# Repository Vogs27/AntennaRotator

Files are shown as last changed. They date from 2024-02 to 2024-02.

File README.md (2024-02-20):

# AntennaRotator
This is an improved antenna rotor based on [Satnogs Project rotor V3.1](https://wiki.satnogs.org/SatNOGS_Rotator_v3). It uses the same mechanics but a different custom made controller.

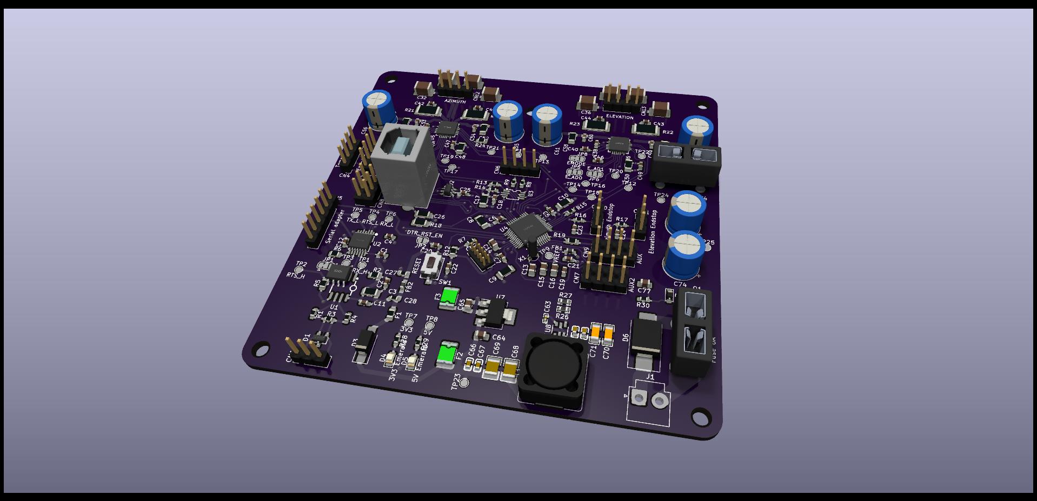
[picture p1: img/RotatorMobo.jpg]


The board uses an ARM based microcontroller (SAMD21) at 48MHz, giving more headroom for future developements. It uses the Arduino Zero core to ease the programming stage. 
TMC2209 are used as drivers to provide a silent experience.

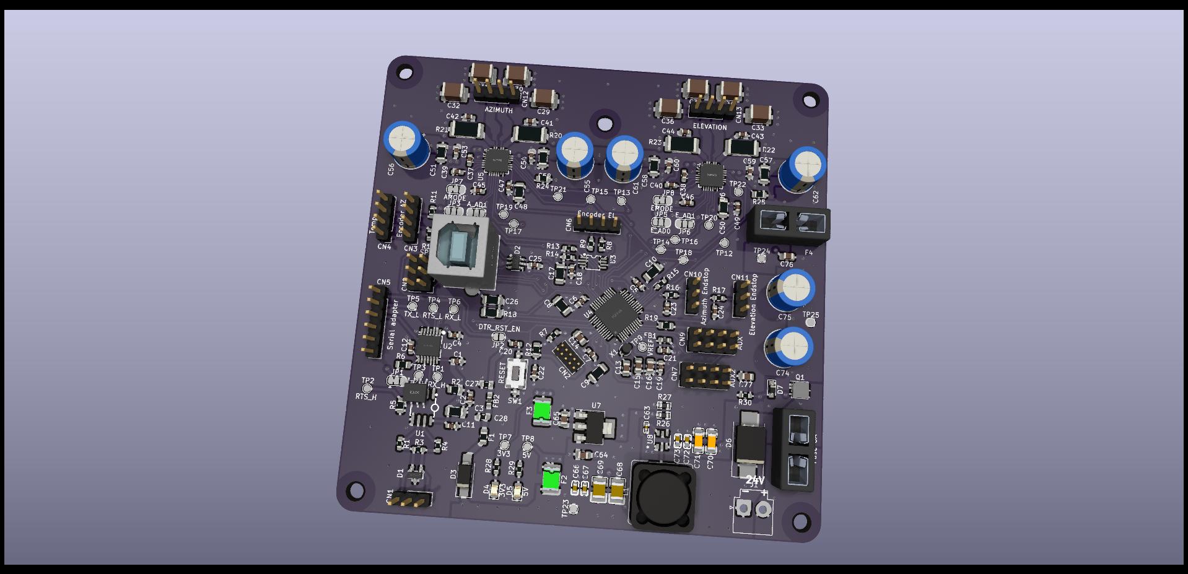
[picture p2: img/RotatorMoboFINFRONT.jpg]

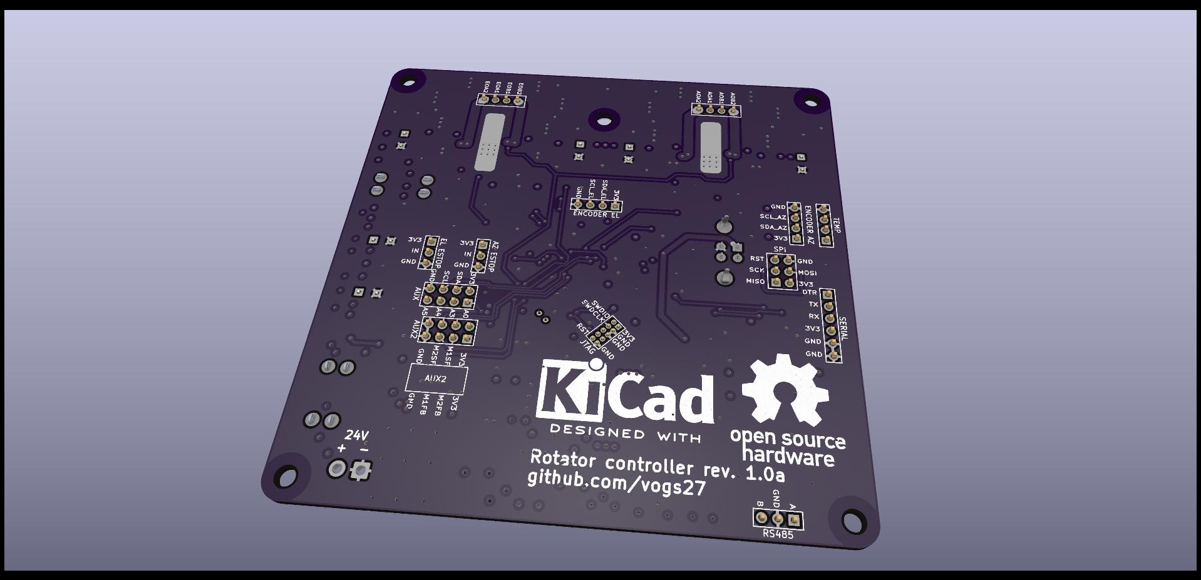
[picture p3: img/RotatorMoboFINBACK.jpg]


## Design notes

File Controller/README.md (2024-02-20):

# Controller board

This is the first version of the controller board.
It's a 100mmx100mm 4 layer PCB.

An interactive bom is provided inside ibom folder.
Grbl files are in production folder together with a BOM file. Some LCSC components code are provided for reference.

The board was manufactured at JLCPCB.

## ToDo

Ground trace in TMC2209 is not connected to both ground vias but just to one. After testing this doesn't seems a problem.

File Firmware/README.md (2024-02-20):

# Rotator Firmware

This firmware is based on [SatNOGS Rotator Controller](https://gitlab.com/librespacefoundation/satnogs/satnogs-rotator-firmware) and is in a very alpha state: use it with caution!
A lot of safety features are still not implemented (watchdog, overheating protection).

## Instructions

In order to use this code, you need to install:
 * [AccelStepper library](http://www.airspayce.com/mikem/arduino/AccelStepper/index.html)
 * [TMCStepper library](https://github.com/teemuatlut/TMCStepper)
 * Download Arduino IDE (tested with 1.8.5)

#### Burn optiboot

Only with SWD programming:

* Jlink like programmer
* Arduino Micro as DAP device

Connect the programmer to the SWD port on the board. Using Arduino IDE, select Arduino Zero (programming port), then burn bootloader. Wait while flashing the bootloader and disconnect the programmer.

#### Upload the code

Connect a USB cable to the controller board. Select Arduino Zero (native port) in Arduino IDE. Open the main firmware file (.ino) in Arduino IDE and press Upload. Wait while flashing the firmware. Disconnect USB cable.

## Testing with hamlib - rotctl or with Serial Monitor

Connect the PC with contreller via RS485 to USB by using the right converter.
Use commands of rotctl:

```
rotctl -m 204 -s 19200 -r /dev/ttyUSB1 -vvvvv
```

Replace the /dev/ttyUSB1 with the device which is connected to PC.

Use commands of easycomm 3:

Send directly commands of easycomm 3 as described in Easycomm implemantation section.

## Use with Gpredict
Configure Gpredict and launch hamlib deamon with: 
```
rotctld -m 202 -r COM7 -s 19200 -T 127.0.0.1 -t 4533 -C timeout=500 -C retry=0 > pause
```
Replace the COM7 with the device which is connected to PC.

## Easycomm implemantation

* AZ, Azimuth, number - 1 decimal place [deg]
* EL, Elevation, number - 1 decimal place [deg]
* SA, Stop azimuth moving
* SE, Stop elevation moving
* RESET, Move to home position
* PARK, Move to park position
* IP, Read an input, number
    * Temperature = 0
    * SW1 = 1
    * SW2 = 2
    * Encoder1 = 3
    * Encoder2 = 4
    * Load of M1/AZ = 5
    * Load of M2/EL = 6
    * Speed of M1/AZ (DPS) = 7
    * Speed of M2/EL (DPS) = 8
* VE, Request Version
* GS, Get status register, number
    * idle = 1
    * moving = 2
    * pointing = 4
    * error = 8
* GE, Get error register, number
    * no_error = 1
    * sensor_error = 2
    * homing_error = 4
    * motor_error = 8
    * over_temperature = 12
    * wdt_error = 16
* VL, Velocity Left ,number [mdeg/s]
* VR, Velocity Right, number [mdeg/s]
* VU, Velocity Up, number [mdeg/s]
* VD, Velocity Down, number [mdeg/s]
* CR, Read config, register [0-x]
    * Gain P for M1/AZ = 1
    * Gain I for M1/AZ = 2
    * Gain D for M1/AZ = 3
    * Gain P for M2/EL = 4
    * Gain I for M2/EL = 5
    * Gain D for M2/EL = 6
    * Azimuth park position = 7
    * Elevation park position = 8
    * Control mode (position = 0, speed = 1) = 9
* CW, Write config, register [0-x]
    * Gain P for M1/AZ = 1
    * Gain I for M1/AZ = 2
    * Gain D for M1/AZ = 3
    * Gain P for M2/EL = 4
    * Gain I for M2/EL = 5
    * Gain D for M2/EL = 6
    * Azimuth park position = 7
    * Elevation park position = 8
    * This reg is set from Vx commands control mode (position = 0, speed = 1) = 9
* RB, command to reboot controller

## Pins Configuration

```
M1IN1 10, Step or PWM1
M1IN2 9, Direction or PWM2
M1SF  7, Status flag
M1FB  A1, Load measurment

M2IN1 11, Step or PWM1
M2IN2 3, Direction or PWM2
M2SF  6, Status flag
M2FB  A0, Load measurment

MOTOR_EN 8, Enable/Disable motors

SW1 5, Endstop for axis 1
SW2 4, Endstop for axis 2

RS485_DIR 2, RS485 Half Duplex direction pin

SDA_PIN 3, Data I2C pin
SCL_PIN 4, Clock I2C pin

PIN12 12, Digital output pin
PIN13 13, Digital output pin
A2    A2, Analog input pin
A3    A3, Analog input pin
```

## TODO

* Implement overheating protection and overheating warning
* Implement watchdog
* Replace blocking delay with non-blocking delay in easycomm implementation.
* Remove PID related stuff (not used with steppers)

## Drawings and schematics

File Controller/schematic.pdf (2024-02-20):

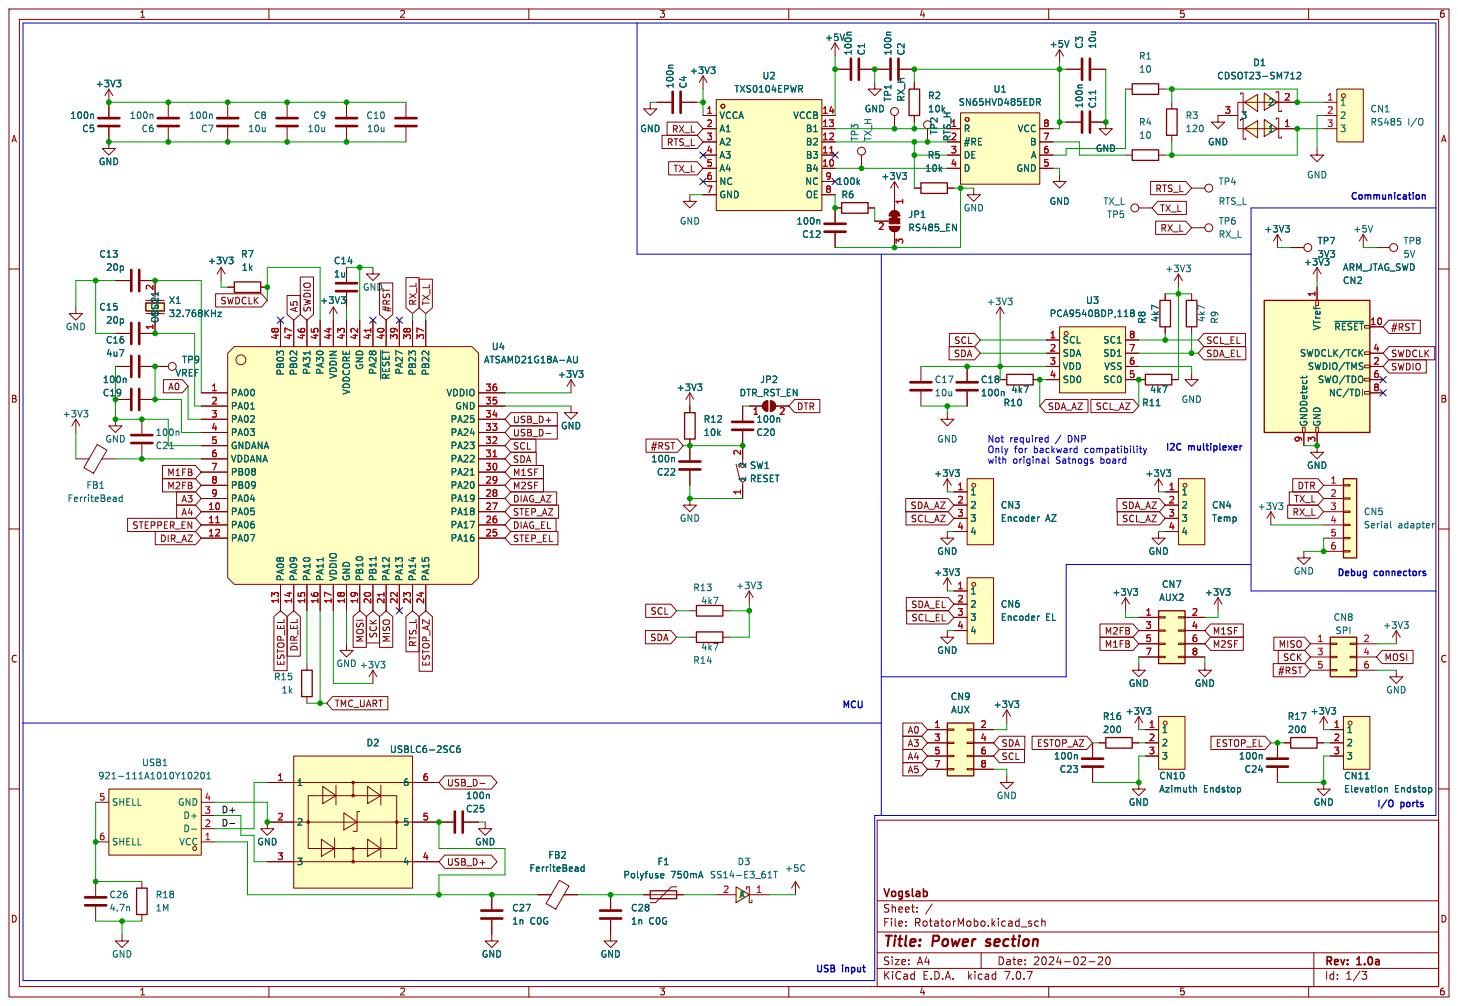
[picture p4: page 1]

3 SWDCLK/TCK 4 SWO/TDO 6 NC/TDI 8 GNDDetect 9 CN2 ARM_JTAG_SWD +3V3 C21

3 SWDCLK/TCK 4 SWO/TDO 6 NC/TDI 8 GNDDetect 9 +3V3 GND

File: RotatorMobo.kicad_sch Sheet: / Vogslab

Id: 1/3 Title: Power section

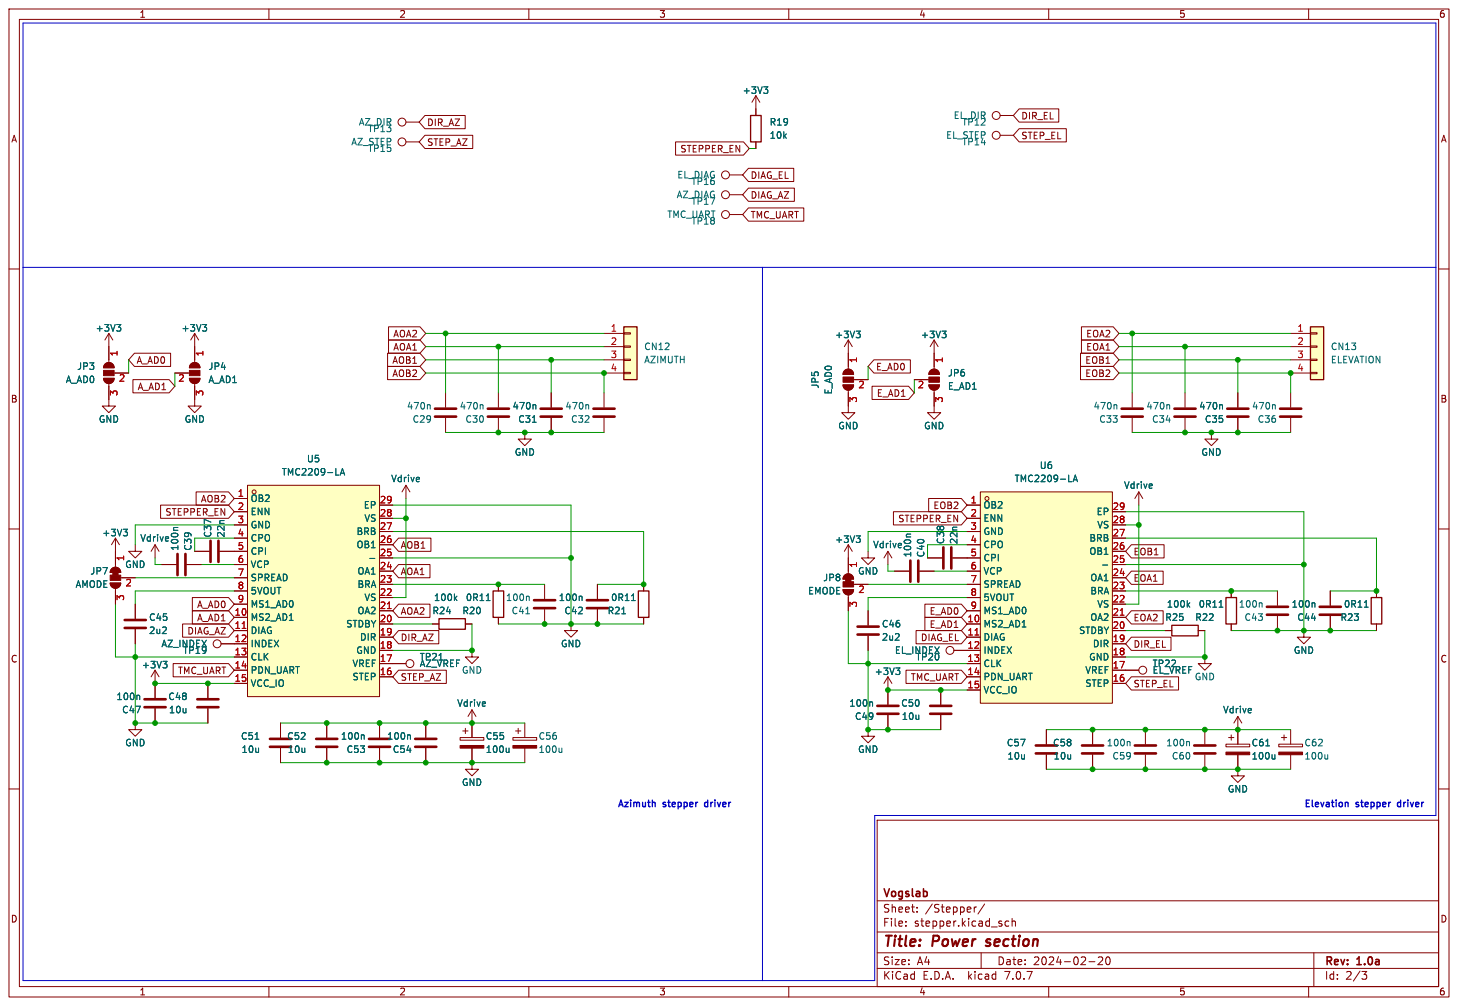
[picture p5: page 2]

- 25 OB1 26 BRB 27 VS 28 EP 29 GND 3 CPO 4 CPI 5 VCP 6 SPREAD 7

File: stepper.kicad_sch Sheet: /Stepper/
Id: 2/3 Title: Power section

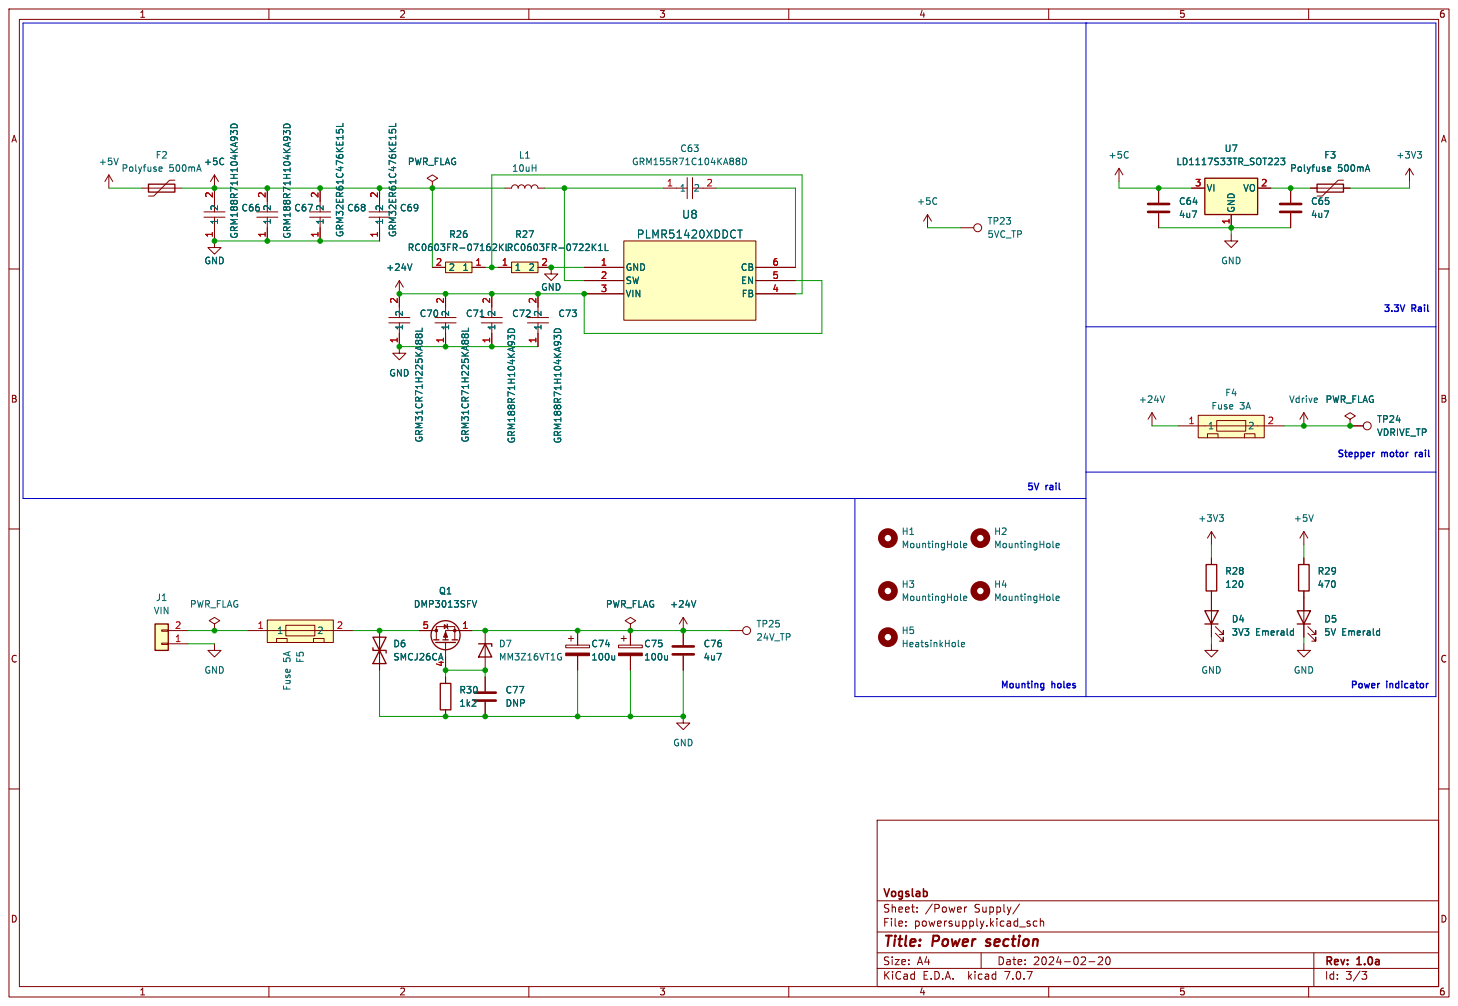
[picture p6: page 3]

Id: 3/3 Title: Power section

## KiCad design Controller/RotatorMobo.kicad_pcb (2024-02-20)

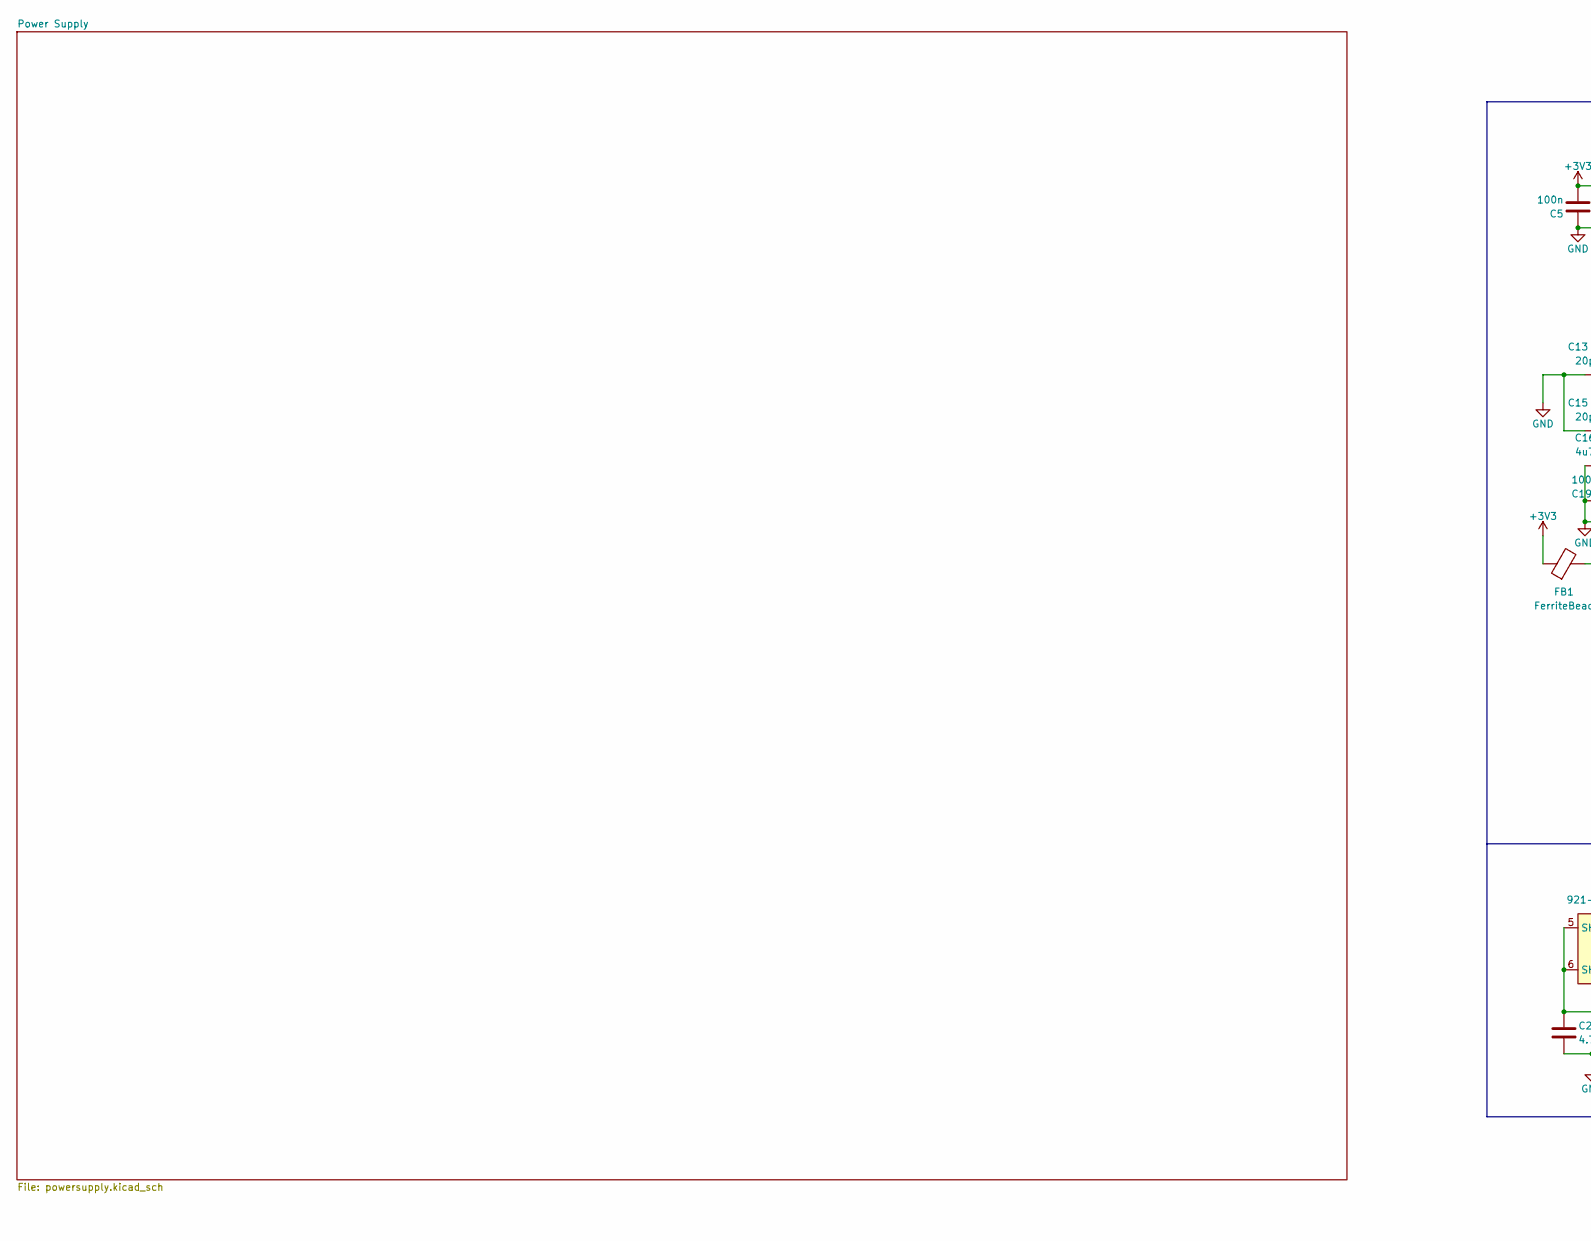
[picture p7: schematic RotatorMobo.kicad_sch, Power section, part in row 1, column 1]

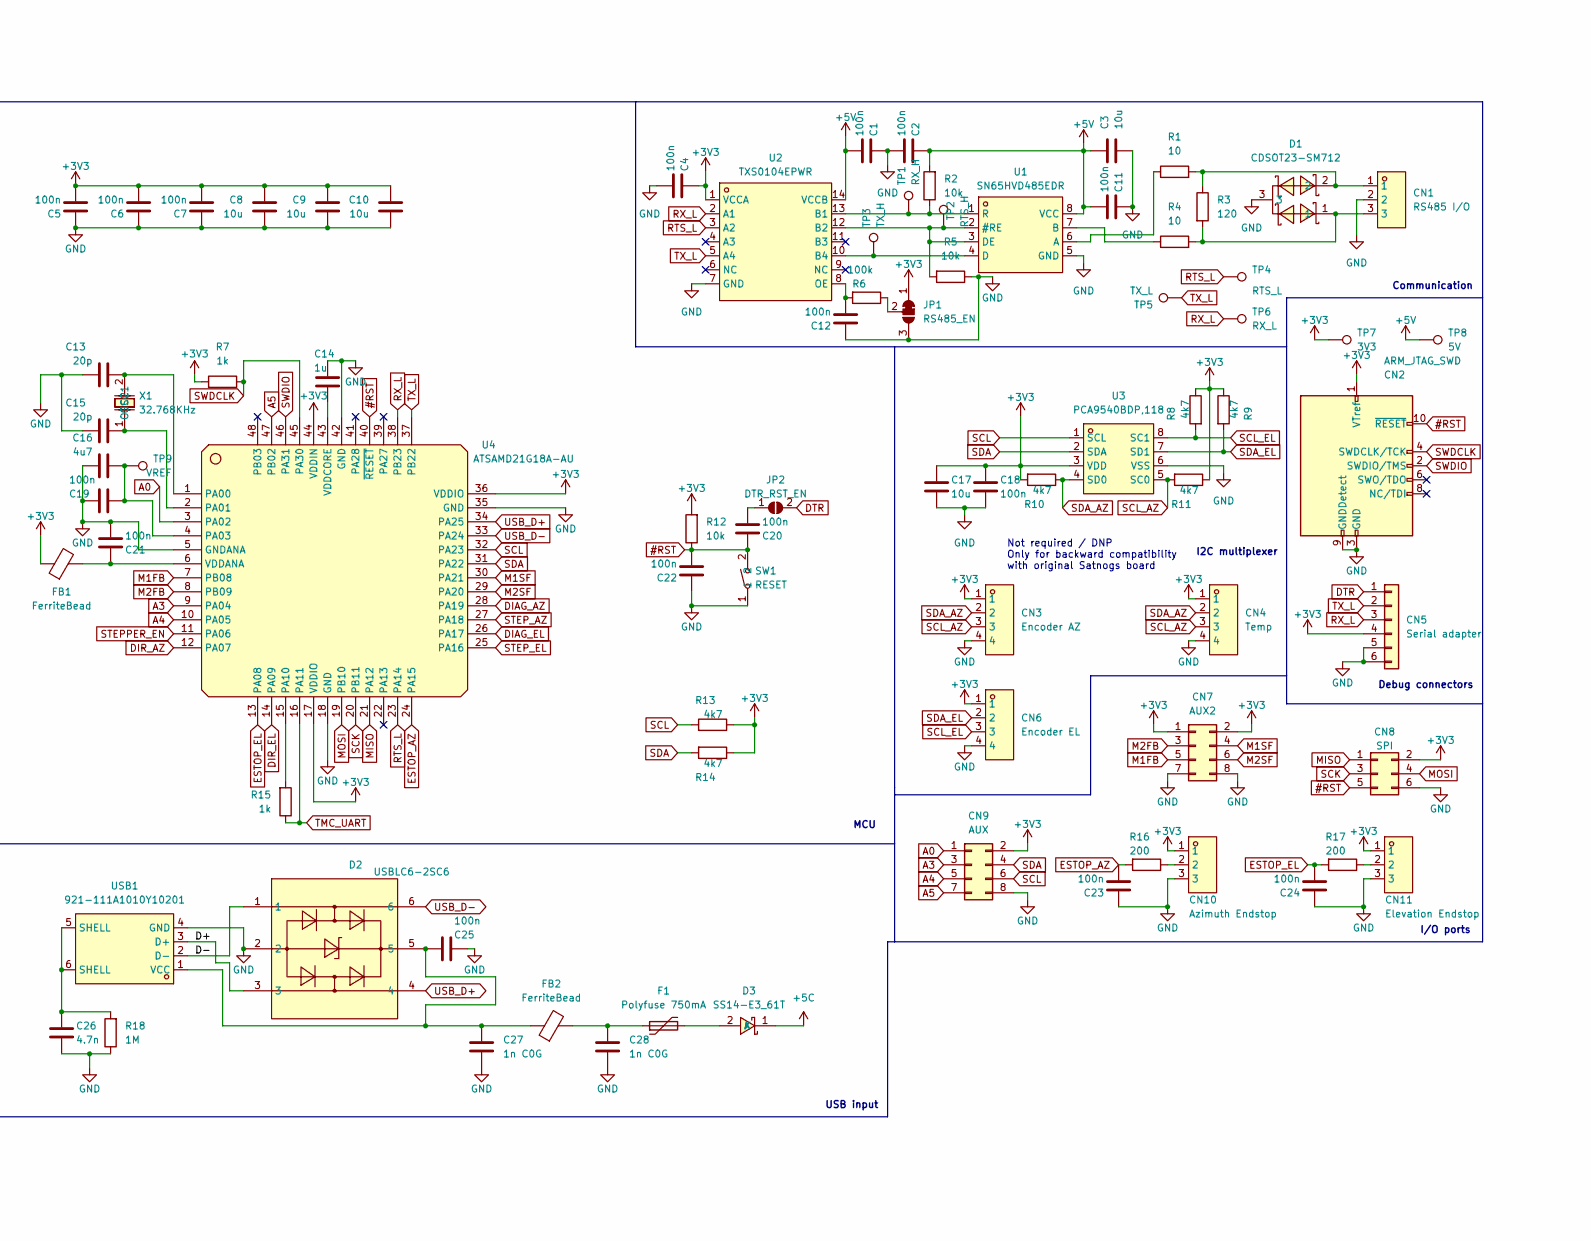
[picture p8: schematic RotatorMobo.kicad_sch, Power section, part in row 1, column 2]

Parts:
C1, C2, C4, C5, C6, C7, C11, C12, C18, C19, C20, C21, C22, C23, C24, C25: 100n; C_0603_1608Metric_Pad1.08x0.95mm_HandSolder; LCSC_id C1591
C3, C8, C9, C10, C17: 10u; R_1206_3216Metric_Pad1.30x1.75mm_HandSolder; LCSC_id C89632
C13, C15: 20p; C_0805_2012Metric_Pad1.18x1.45mm_HandSolder; LCSC_id C1798
C14: 1u; C_0805_2012Metric_Pad1.18x1.45mm_HandSolder; LCSC_id C116352
C16: 4u7; C_0805_2012Metric_Pad1.18x1.45mm_HandSolder; LCSC_id C98192
C26: 4.7n; R_1206_3216Metric_Pad1.30x1.75mm_HandSolder; LCSC_id C571063
C27, C28: 1n C0G; R_0603_1608Metric_Pad0.98x0.95mm_HandSolder; LCSC_id C3909020
CN1: RS485 I/O; PinHeader_1x03_P2.54mm_Vertical; LCSC Part C5341202
CN2: ARM_JTAG_SWD; PinHeader_2x05_P1.27mm_Vertical
CN3: Encoder AZ; PinHeader_1x04_P2.54mm_Vertical; LCSC Part C722867
CN4: Temp; PinHeader_1x04_P2.54mm_Vertical; LCSC Part C722867
CN5: Serial adapter; PinHeader_1x06_P2.54mm_Vertical
CN6: Encoder EL; PinHeader_1x04_P2.54mm_Vertical; LCSC Part C722867
CN7: AUX2; PinHeader_2x04_P2.54mm_Vertical
CN8: SPI; PinHeader_2x03_P2.54mm_Vertical
CN9: AUX; PinHeader_2x04_P2.54mm_Vertical
CN10: Azimuth Endstop; PinHeader_1x03_P2.54mm_Vertical; LCSC Part C5341202
CN11: Elevation Endstop; PinHeader_1x03_P2.54mm_Vertical; LCSC Part C5341202
D1: CDSOT23-SM712; SOT-23_L2.9-W1.3-P1.90-LS2.4-BR; LCSC Part C404012
D2: USBLC6-2SC6; SOT-23-6_L2.9-W1.6-P0.95-LS2.8-BL; LCSC Part C7519
D3: SS14-E3_61T; D_SMA_Handsoldering; LCSC Part C47460
F1: Polyfuse 750mA; Fuse_0805_2012Metric_Pad1.15x1.40mm_HandSolder; LCSC_id C883111
FB1, FB2: FerriteBead; L_0603_1608Metric_Pad1.05x0.95mm_HandSolder; MPN BLM18PG471SN1; LCSC ID C97853
JP1: RS485_EN; SolderJumper-3_P1.3mm_Bridged12_RoundedPad1.0x1.5mm
JP2: DTR_RST_EN; SolderJumper-2_P1.3mm_Open_RoundedPad1.0x1.5mm
R1, R4: 10; R_0603_1608Metric_Pad0.98x0.95mm_HandSolder; LCSC_id C22859
R2, R5, R12: 10k; R_0805_2012Metric_Pad1.20x1.40mm_HandSolder; LCSC_id C25612
R3: 120; R_0603_1608Metric_Pad0.98x0.95mm_HandSolder; LCSC_id C2906988
R6: 100k; R_0805_2012Metric_Pad1.20x1.40mm_HandSolder; LCSC_id C25611
R7, R15: 1k; R_0603_1608Metric_Pad0.98x0.95mm_HandSolder; LCSC_id C21190
R8, R9, R10, R11, R13, R14: 4k7; R_0603_1608Metric_Pad0.98x0.95mm_HandSolder; LCSC_id C25999
R16, R17: 200; R_0603_1608Metric_Pad0.98x0.95mm_HandSolder; LCSC_id C103389
R18: 1M; R_1206_3216Metric_Pad1.30x1.75mm_HandSolder; LCSC_id C175518
SW1: RESET; SW-SMD_L6.1-W3.5-LS8.0; LCSC Part C5117870
TP1: RX_H; TestPoint_Pad_D1.5mm
TP2: RTS_H; TestPoint_Pad_D1.5mm
TP3: TX_H; TestPoint_Pad_D1.5mm
TP4: RTS_L; TestPoint_Pad_D1.5mm
TP5: TX_L; TestPoint_Pad_D1.5mm
TP6: RX_L; TestPoint_Pad_D1.5mm
TP7: 3V3; TestPoint_Pad_D1.5mm
TP8: 5V; TestPoint_Pad_D1.5mm
TP9: VREF; TestPoint_Pad_D1.5mm
U1: SN65HVD485EDR; SOIC-8_L5.0-W4.0-P1.27-LS6.0-BL; LCSC Part C27899
U2: TXS0104EPWR; TSSOP-14_L5.0-W4.4-P0.65-LS6.4-BL; LCSC Part C44955
U3: PCA9540BDP,118; TSSOP-8_L3.0-W3.0-P0.65-LS4.9-BL; LCSC Part C2652901
U4: ATSAMD21G18A-AU; TQFP-48_L7.0-W7.0-P0.50-LS9.0-BL; LCSC Part C78624
USB1: 921-111A1010Y10201; USB-B-TH_921-111A1010Y10201; LCSC Part C2763094
X1: 32.768KHz; OSC-TH_BD1.9-P0.70; LCSC Part C403947

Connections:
#RST: C20.2, C22.1, CN2.10 (~RESET), CN8.5, R12.1, SW1.2, U4.40 (~RESET)
+3V3: C4.2, C5.1, C6.1, C7.1, C8.2, C9.2, C10.2, C17.2, C18.2, CN2.1 (VTref), CN3.1, CN4.1, CN5.4, CN6.1, CN7.1, CN7.2, CN8.2, CN9.2, CN10.1, CN11.1, FB1.1, JP1.1 (A), R7.2, R8.1, R9.1, R10.2, R11.1, R12.2, R13.1, R14.1, TP7.1, U2.1 (VCCA), U3.3 (VDD), U4.17 (VDDIO), U4.36 (VDDIO), U4.44 (VDDIN); also elsewhere on the board
+5C: D3.1 (K); also elsewhere on the board
+5V: C1.1, C2.2, C3.2, C11.1, R2.2, TP8.1, U1.8 (VCC), U2.14 (VCCB); also elsewhere on the board
/D+: D2.3, USB1.3 (D+)
/D-: D2.1, USB1.2 (D-)
A0: CN9.1, U4.3 (PA02)
A3: CN9.3, U4.9 (PA04)
A4: CN9.5, U4.10 (PA05)
A5: CN9.7, U4.47 (PB02)
DIAG_AZ: U4.28 (PA19); also elsewhere on the board
DIAG_EL: U4.26 (PA17); also elsewhere on the board
DIR_AZ: U4.12 (PA07); also elsewhere on the board
DIR_EL: U4.14 (PA09); also elsewhere on the board
DTR: CN5.1, JP2.2 (B)
ESTOP_AZ: C23.1, R16.2, U4.24 (PA15)
ESTOP_EL: C24.1, R17.2, U4.13 (PA08)
GND: C1.2, C2.1, C3.1, C4.1, C5.2, C6.2, C7.2, C8.1, C9.1, C10.1, C11.2, C12.2, C13.1, C14.2, C15.1, C16.1, C17.1, C18.1, C19.1, C21.1, C22.2, C23.2, C24.2, C25.2, C26.1, C27.1, C28.1, CN1.2, CN2.3 (GND), CN2.5 (GND), CN2.9 (GNDDetect), CN3.4, CN4.4, CN5.5, CN5.6, CN6.4, CN7.7, CN7.8, CN8.6, CN9.8, CN10.3, CN11.3, D1.3, D2.2, JP1.3 (B), R5.1, R18.1, SW1.1, U1.5 (GND), U2.7 (GND), U3.6 (VSS), U4.5 (GNDANA), U4.18 (GND), U4.35 (GND), U4.42 (GND), USB1.4 (GND); also elsewhere on the board
M1FB: CN7.5, U4.7 (PB08)
M1SF: CN7.4, U4.30 (PA21)
M2FB: CN7.3, U4.8 (PB09)
M2SF: CN7.6, U4.29 (PA20)
MISO: CN8.1, U4.21 (PA12)
MOSI: CN8.4, U4.19 (PB10)
unnamed: C26.2, R18.2, USB1.5 (SHELL), USB1.6 (SHELL)
unnamed: C28.2, F1.1, FB2.2
unnamed: CN1.1, D1.2, R1.2, R3.1
unnamed: CN1.3, D1.1, R3.2, R4.2
unnamed: CN10.2, R16.1
unnamed: CN11.2, R17.1
unnamed: D3.2 (A), F1.2
unnamed: JP1.2 (C), R6.1
unnamed: C20.1, JP2.1 (A)
unnamed: R5.2, TP2.1, U1.2 (#RE), U1.3 (DE), U2.12 (B2)
unnamed: R1.1, U1.6 (A)
unnamed: R4.1, U1.7 (B)
unnamed: TP3.1, U1.4 (D), U2.10 (B4)
unnamed: R2.1, TP1.1, U1.1 (R), U2.13 (B1)
unnamed: C12.1, R6.2, U2.8 (OE)
unnamed: C13.2, U4.1 (PA00), X1.2 (OSC2)
unnamed: C15.2, U4.2 (PA01), X1.1 (OSC1)
unnamed: C16.2, C19.2, TP9.1, U4.4 (PA03)
unnamed: R15.2, U4.15 (PA10)
unnamed: C21.2, FB1.2, U4.6 (VDDANA)
unnamed: C14.1, U4.43 (VDDCORE)
unnamed: C25.1, C27.2, D2.5, FB2.1, USB1.1 (VCC)
RTS_L: TP4.1, U2.3 (A2), U4.23 (PA14)
RX_L: CN5.3, TP6.1, U2.2 (A1), U4.38 (PB23)
SCK: CN8.3, U4.20 (PB11)
SCL: CN9.6, R13.2, U3.1 (SCL), U4.32 (PA23)
SCL_AZ: CN3.3, CN4.3, R11.2, U3.5 (SC0)
SCL_EL: CN6.3, R8.2, U3.8 (SC1)
SDA: CN9.4, R14.2, U3.2 (SDA), U4.31 (PA22)
SDA_AZ: CN3.2, CN4.2, R10.1, U3.4 (SD0)
SDA_EL: CN6.2, R9.2, U3.7 (SD1)
STEPPER_EN: U4.11 (PA06); also elsewhere on the board
STEP_AZ: U4.27 (PA18); also elsewhere on the board
STEP_EL: U4.25 (PA16); also elsewhere on the board
SWDCLK: CN2.4 (SWDCLK/TCK), R7.1, U4.45 (PA30)
SWDIO: CN2.2 (SWDIO/TMS), U4.46 (PA31)
TMC_UART: R15.1, U4.16 (PA11); also elsewhere on the board
TX_L: CN5.2, TP5.1, U2.5 (A4), U4.37 (PB22)
USB_D+: D2.4, U4.34 (PA25)
USB_D-: D2.6, U4.33 (PA24)

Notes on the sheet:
Communication
I2C multiplexer
Debug connectors
I/O ports
MCU
USB input
Not required / DNP Only for backward compatibility with original Satnogs board

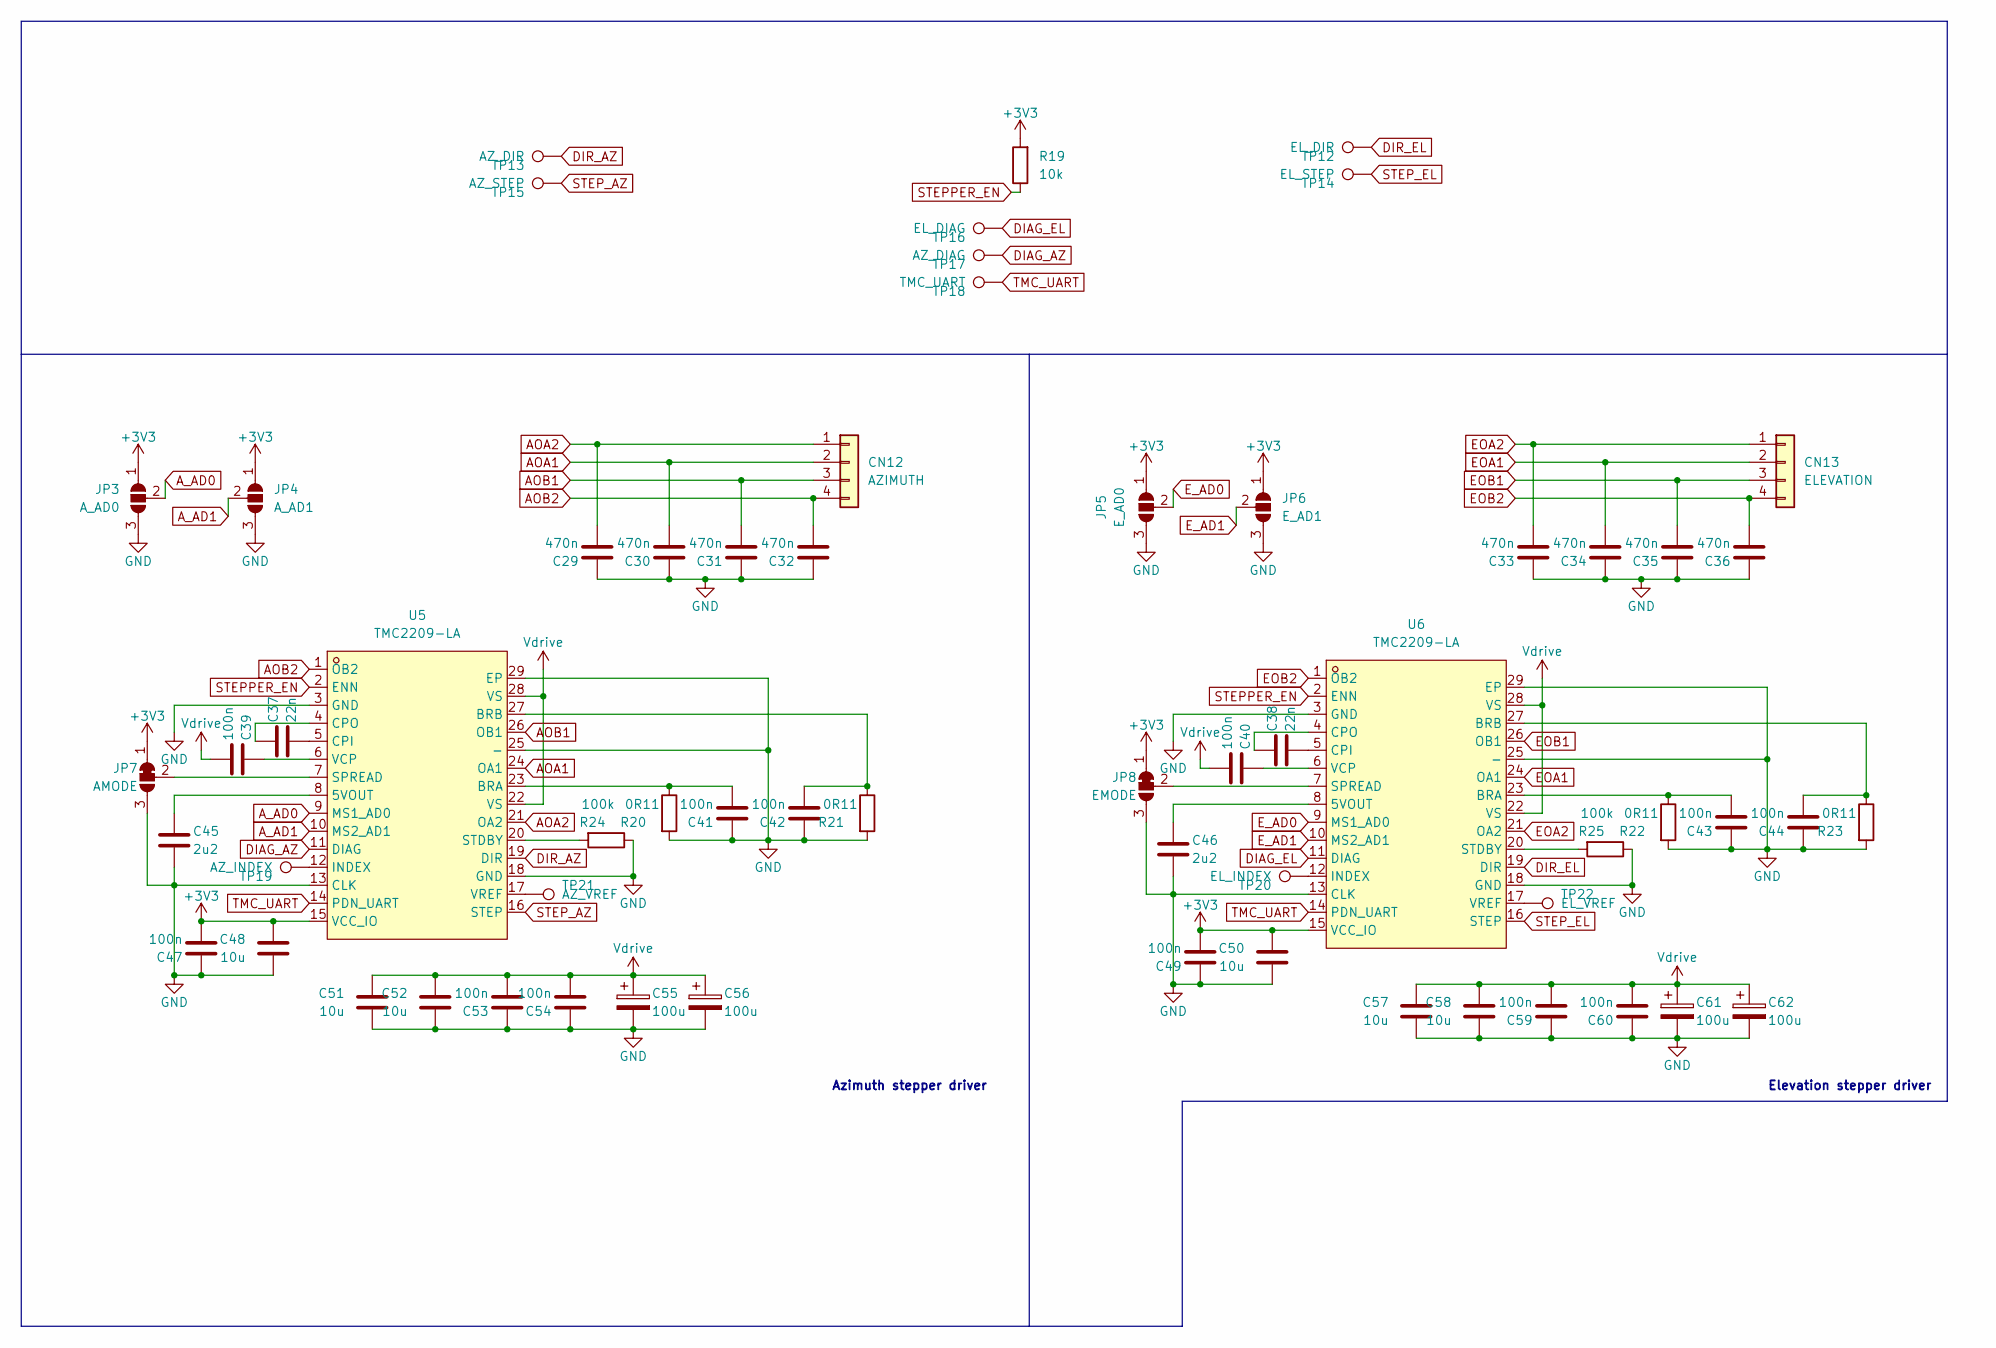
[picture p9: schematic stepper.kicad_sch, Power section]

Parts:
C29, C30, C31, C32, C33, C34, C35, C36: 470n; C_1812_4532Metric_Pad1.57x3.40mm_HandSolder; LCSC_id C152994
C37, C38: 22n; C_0603_1608Metric_Pad1.08x0.95mm_HandSolder; LCSC_id C21122
C39, C40, C41, C42, C43, C44, C47, C49, C53, C54, C59, C60: 100n; C_0603_1608Metric_Pad1.08x0.95mm_HandSolder; LCSC_id C1591
C45, C46: 2u2; C_0603_1608Metric_Pad1.08x0.95mm_HandSolder; LCSC_id C23630
C48, C50, C51, C52, C57, C58: 10u; R_1206_3216Metric_Pad1.30x1.75mm_HandSolder; LCSC_id C89632
C55, C56, C61, C62: 100u; CP_Radial_D8.0mm_P3.50mm
CN12: AZIMUTH; PinHeader_1x04_P2.54mm_Vertical
CN13: ELEVATION; PinHeader_1x04_P2.54mm_Vertical
JP3: A_AD0; SolderJumper-3_P1.3mm_Open_RoundedPad1.0x1.5mm
JP4: A_AD1; SolderJumper-3_P1.3mm_Open_RoundedPad1.0x1.5mm
JP5: E_AD0; SolderJumper-3_P1.3mm_Open_RoundedPad1.0x1.5mm
JP6: E_AD1; SolderJumper-3_P1.3mm_Open_RoundedPad1.0x1.5mm
JP7: AMODE; SolderJumper-3_P1.3mm_Bridged12_RoundedPad1.0x1.5mm
JP8: EMODE; SolderJumper-3_P1.3mm_Bridged12_RoundedPad1.0x1.5mm
R19: 10k; R_0805_2012Metric_Pad1.20x1.40mm_HandSolder; LCSC_id C25612
R20, R21, R22, R23: 0R11; R_2512_6332Metric_Pad1.40x3.35mm_HandSolder; LCSC_id C333708
R24, R25: 100k; R_0805_2012Metric_Pad1.20x1.40mm_HandSolder; LCSC_id C25611
TP12: EL_DIR; TestPoint_Pad_D1.5mm
TP13: AZ_DIR; TestPoint_Pad_D1.5mm
TP14: EL_STEP; TestPoint_Pad_D1.5mm
TP15: AZ_STEP; TestPoint_Pad_D1.5mm
TP16: EL_DIAG; TestPoint_Pad_D1.5mm
TP17: AZ_DIAG; TestPoint_Pad_D1.5mm
TP18: TMC_UART; TestPoint_Pad_D1.5mm
TP19: AZ_INDEX; TestPoint_Pad_D1.5mm
TP20: EL_INDEX; TestPoint_Pad_D1.5mm
TP21: AZ_VREF; TestPoint_Pad_D1.5mm
TP22: EL_VREF; TestPoint_Pad_D1.5mm
U5, U6: TMC2209-LA; QFN-28_L5.0-W5.0-P0.50-BL-EP; LCSC Part C465949

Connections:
+3V3: C47.1, C48.2, C49.1, C50.2, JP3.1 (A), JP4.1 (A), JP5.1 (A), JP6.1 (A), JP7.1 (A), JP8.1 (A), R19.2, U5.15 (VCC_IO), U6.15 (VCC_IO); also elsewhere on the board
AOA1: C30.1, CN12.2, U5.24 (OA1)
AOA2: C29.1, CN12.1, U5.21 (OA2)
AOB1: C31.1, CN12.3, U5.26 (OB1)
AOB2: C32.1, CN12.4, U5.1 (OB2)
A_AD0: JP3.2 (C), U5.9 (MS1_AD0)
A_AD1: JP4.2 (C), U5.10 (MS2_AD1)
DIAG_AZ: TP17.1, U5.11 (DIAG); also elsewhere on the board
DIAG_EL: TP16.1, U6.11 (DIAG); also elsewhere on the board
DIR_AZ: TP13.1, U5.19 (DIR); also elsewhere on the board
DIR_EL: TP12.1, U6.19 (DIR); also elsewhere on the board
EOA1: C34.1, CN13.2, U6.24 (OA1)
EOA2: C33.1, CN13.1, U6.21 (OA2)
EOB1: C35.1, CN13.3, U6.26 (OB1)
EOB2: C36.1, CN13.4, U6.1 (OB2)
E_AD0: JP5.2 (C), U6.9 (MS1_AD0)
E_AD1: JP6.2 (C), U6.10 (MS2_AD1)
GND: C29.2, C30.2, C31.2, C32.2, C33.2, C34.2, C35.2, C36.2, C41.2, C42.2, C43.2, C44.2, C45.1, C46.1, C47.2, C48.1, C49.2, C50.1, C51.1, C52.1, C53.2, C54.2, C55.2, C56.2, C57.1, C58.1, C59.2, C60.2, C61.2, C62.2, JP3.3 (B), JP4.3 (B), JP5.3 (B), JP6.3 (B), JP7.3 (B), JP8.3 (B), R20.2, R21.2, R22.2, R23.2, R24.1, R25.1, U5.3 (GND), U5.13 (CLK), U5.18 (GND), U5.25 (-), U5.29 (EP), U6.3 (GND), U6.13 (CLK), U6.18 (GND), U6.25 (-), U6.29 (EP); also elsewhere on the board
unnamed: JP7.2 (C), U5.7 (SPREAD)
unnamed: JP8.2 (C), U6.7 (SPREAD)
unnamed: C45.2, U5.8 (5VOUT)
unnamed: C41.1, R20.1, U5.23 (BRA)
unnamed: C42.1, R21.1, U5.27 (BRB)
unnamed: C37.1, U5.5 (CPI)
unnamed: C37.2, U5.4 (CPO)
unnamed: TP19.1, U5.12 (INDEX)
unnamed: R24.2, U5.20 (STDBY)
unnamed: C39.2, U5.6 (VCP)
unnamed: TP21.1, U5.17 (VREF)
unnamed: C46.2, U6.8 (5VOUT)
unnamed: C43.1, R22.1, U6.23 (BRA)
unnamed: C44.1, R23.1, U6.27 (BRB)
unnamed: C38.1, U6.5 (CPI)
unnamed: C38.2, U6.4 (CPO)
unnamed: TP20.1, U6.12 (INDEX)
unnamed: R25.2, U6.20 (STDBY)
unnamed: C40.2, U6.6 (VCP)
unnamed: TP22.1, U6.17 (VREF)
STEPPER_EN: R19.1, U5.2 (ENN), U6.2 (ENN); also elsewhere on the board
STEP_AZ: TP15.1, U5.16 (STEP); also elsewhere on the board
STEP_EL: TP14.1, U6.16 (STEP); also elsewhere on the board
TMC_UART: TP18.1, U5.14 (PDN_UART), U6.14 (PDN_UART); also elsewhere on the board
Vdrive: C39.1, C40.1, C51.2, C52.2, C53.1, C54.1, C55.1, C56.1, C57.2, C58.2, C59.1, C60.1, C61.1, C62.1, U5.22 (VS), U5.28 (VS), U6.22 (VS), U6.28 (VS); also elsewhere on the board

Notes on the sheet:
Azimuth stepper driver
Elevation stepper driver

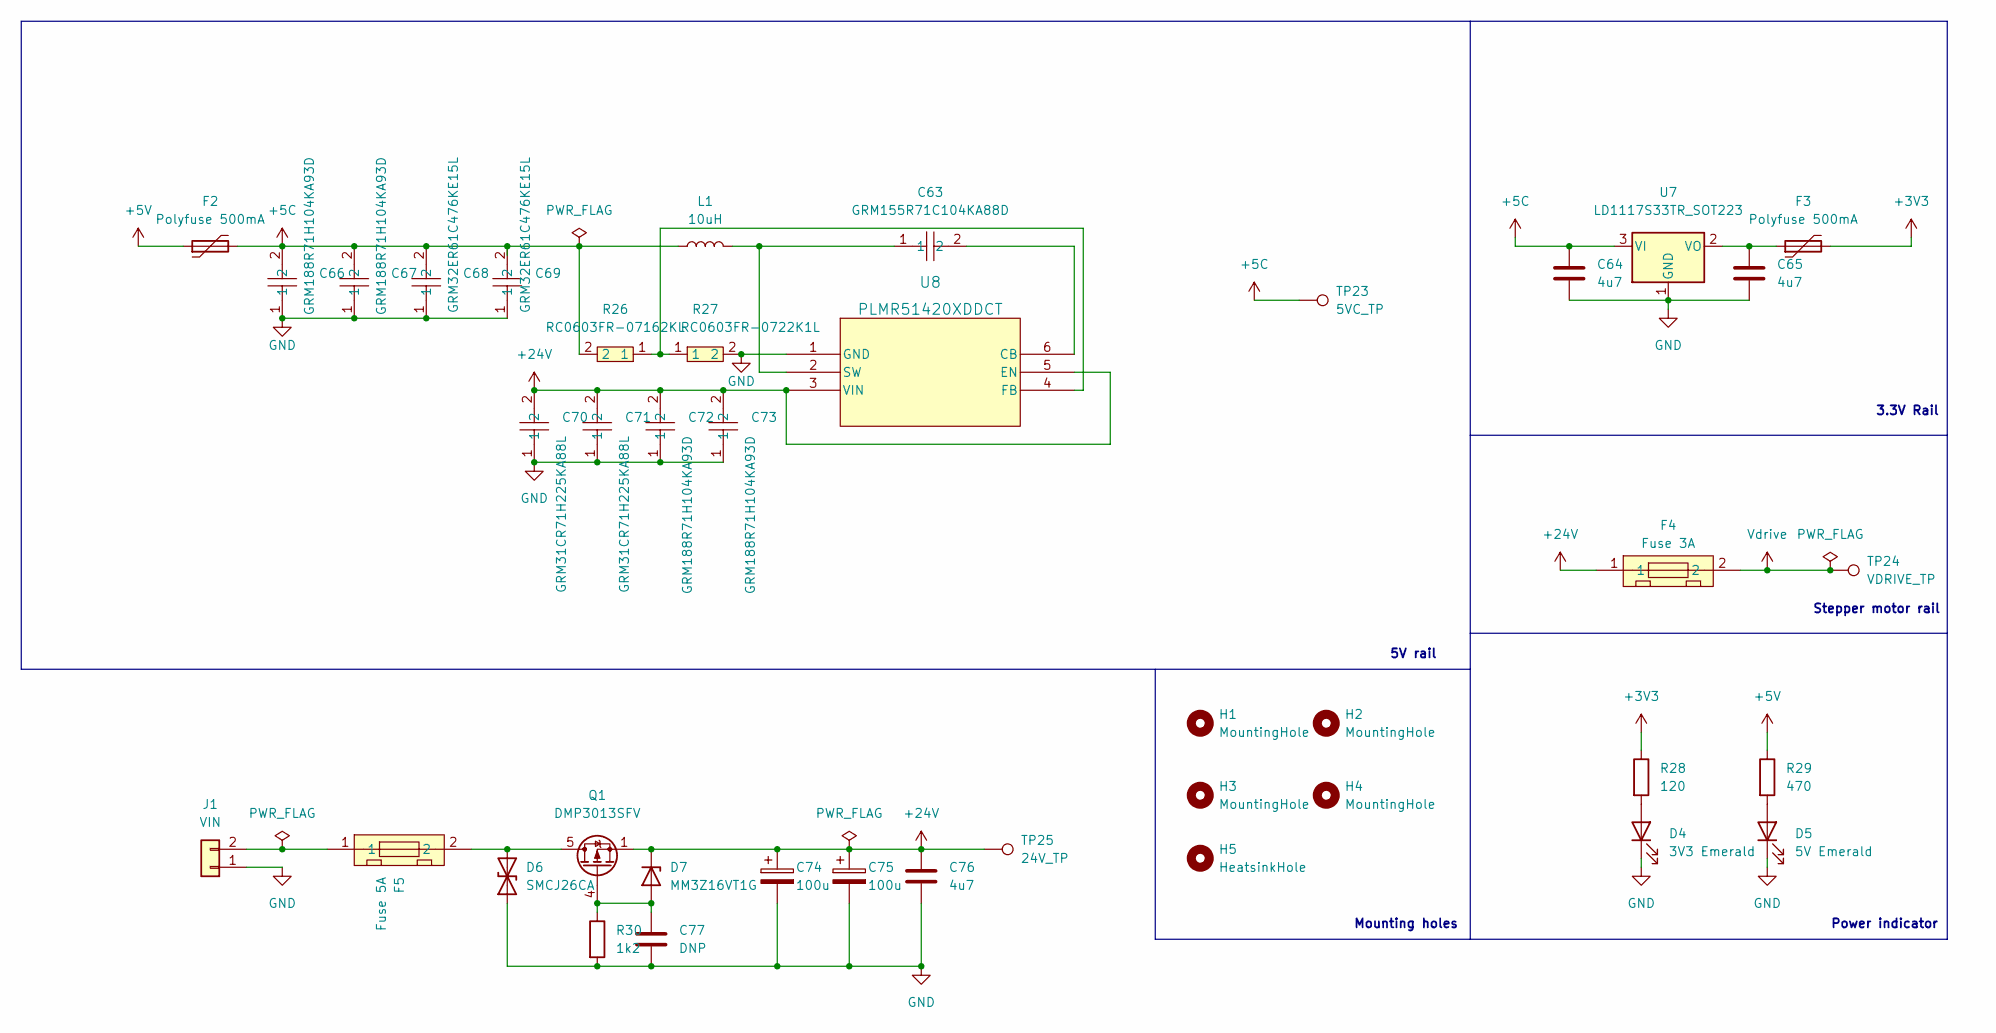
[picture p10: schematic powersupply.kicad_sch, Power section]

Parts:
C63: GRM155R71C104KA88D; C0402; LCSC Part C71629
C64, C65, C76: 4u7; C_0805_2012Metric_Pad1.18x1.45mm_HandSolder; LCSC_id C98192
C66, C67, C72, C73: GRM188R71H104KA93D; C0603; LCSC Part C77055
C68, C69: GRM32ER61C476KE15L; C1210; LCSC Part C77101
C70, C71: GRM31CR71H225KA88L; C1206; LCSC Part C77095
C74, C75: 100u; CP_Radial_D8.0mm_P3.50mm
C77: DNP; C_0805_2012Metric_Pad1.18x1.45mm_HandSolder
D4: 3V3 Emerald; LED_0805_2012Metric_Pad1.15x1.40mm_HandSolder; LCSC_id C965815
D5: 5V Emerald; LED_0805_2012Metric_Pad1.15x1.40mm_HandSolder; LCSC_id C965815
D6: SMCJ26CA; D_SMC_Handsoldering; LCSC_id C151280
D7: MM3Z16VT1G; D_SOD-323_HandSoldering; LCSC_id C150089
F2, F3: Polyfuse 500mA; Fuse_1812_4532Metric_Pad1.30x3.40mm_HandSolder; LCSC_id C2649901
F4: Fuse 3A; FUSE-TH_XF-506P; LCSC_id C2935468
F5: Fuse 5A; FUSE-TH_XF-506P; LCSC_id C2935468
H1, H2, H3, H4: MountingHole; MountingHole_3.2mm_M3
H5: HeatsinkHole; MountingHole_3.2mm_M3
J1: VIN; JST_VH_B2P-VH-B_1x02_P3.96mm_Vertical
L1: 10uH; L_Bourns_SRR1260; LCSC_id C2041557
Q1: DMP3013SFV; Diodes_PowerDI3333-8; LCSC_id C264098
R26: RC0603FR-07162KL; R0603; LCSC Part C165760
R27: RC0603FR-0722K1L; R0603; LCSC Part C137768
R28: 120; R_0603_1608Metric_Pad0.98x0.95mm_HandSolder; LCSC_id C2906988
R29: 470; R_0603_1608Metric_Pad0.98x0.95mm_HandSolder; LCSC_id C5140094
R30: 1k2; R_0603_1608Metric_Pad0.98x0.95mm_HandSolder; LCSC_id C25987
TP23: 5VC_TP; TestPoint_Pad_D1.5mm
TP24: VDRIVE_TP; TestPoint_Pad_D1.5mm
TP25: 24V_TP; TestPoint_Pad_D1.5mm
U7: LD1117S33TR_SOT223; SOT-223-3_TabPin2; LCSC_id C35879
U8: PLMR51420XDDCT; SOT-23-THIN-6_DDC_TEX; LCSC_id C5246146

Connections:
+3V3: F3.2, R28.1; also elsewhere on the board
+5C: C64.1, C66.2, C67.2, C68.2, C69.2, F2.2, L1.1, R26.2, TP23.1, U7.3 (VI); also elsewhere on the board
+5V: F2.1, R29.1; also elsewhere on the board
+24V: C70.2, C71.2, C72.2, C73.2, C74.1, C75.1, C76.1, D7.1 (K), F4.1, Q1.1 (S), Q1.2 (S), Q1.3 (S), TP25.1, U8.3 (VIN), U8.5 (EN)
GND: C64.2, C65.2, C66.1, C67.1, C68.1, C69.1, C70.1, C71.1, C72.1, C73.1, C74.2, C75.2, C76.2, C77.2, D4.1 (K), D5.1 (K), D6.1 (A1), J1.1, R27.2, R30.2, U7.1 (GND), U8.1 (GND); also elsewhere on the board
unnamed: D4.2 (A), R28.2
unnamed: D5.2 (A), R29.2
unnamed: D6.2 (A2), F5.2, Q1.5 (D)
unnamed: C77.1, D7.2 (A), Q1.4 (G), R30.1
unnamed: F5.1, J1.2
unnamed: C65.1, F3.1, U7.2 (VO)
unnamed: C63.2, U8.6 (CB)
unnamed: R26.1, R27.1, U8.4 (FB)
unnamed: C63.1, L1.2, U8.2 (SW)
Vdrive: F4.2, TP24.1; also elsewhere on the board

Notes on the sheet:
Stepper motor rail
5V rail
Mounting holes
3.3V Rail
Power indicator

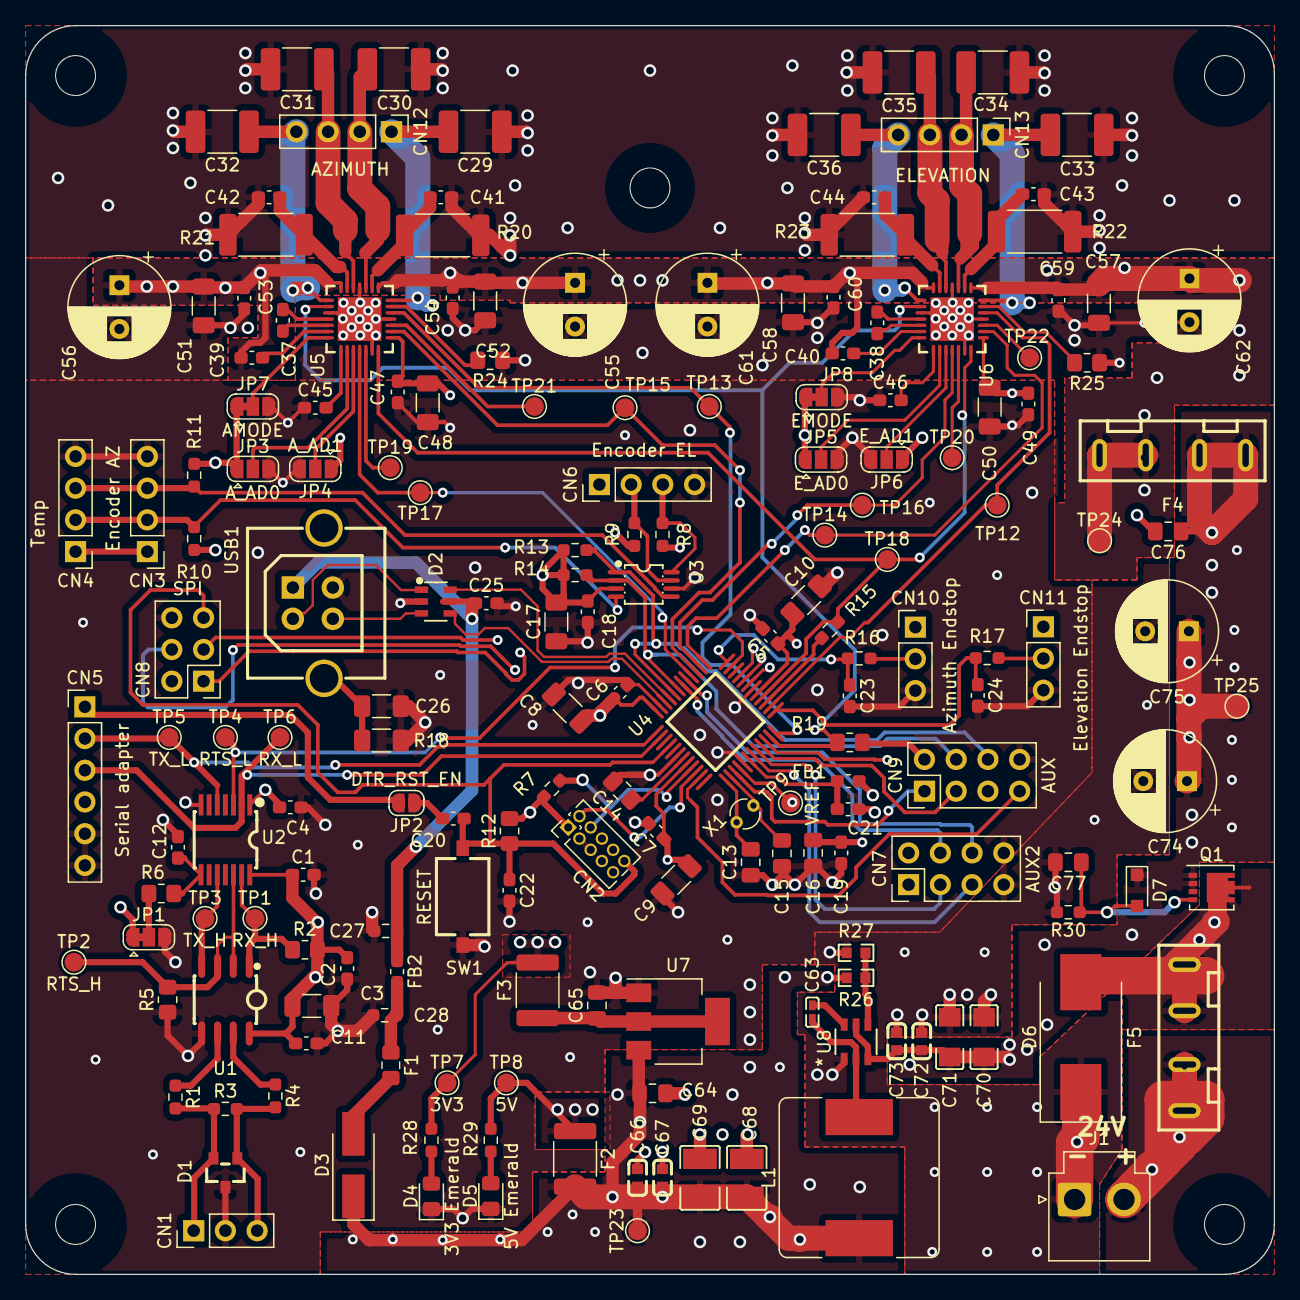
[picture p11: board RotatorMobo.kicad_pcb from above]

Board: 4 copper layers, 100.0 x 100.0 mm, 184 parts (0 on the bottom side), 107 nets.

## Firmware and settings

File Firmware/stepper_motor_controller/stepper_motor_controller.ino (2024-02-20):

/*!
   @file stepper_motor_controller.ino

   This is the documentation for satnogs rotator controller firmware
   for stepper motors configuration. The board (PCB) is placed in
   <a href="https://gitlab.com/librespacefoundation/satnogs/satnogs-rotator-controller">
   satnogs-rotator-controller </a> and is for releases:
   v2.0
   v2.1
   v2.2
   <a href="https://wiki.satnogs.org/SatNOGS_Rotator_Controller"> wiki page </a>

   @section dependencies Dependencies

   This firmware depends on <a href="http://www.airspayce.com/mikem/arduino/AccelStepper/index.htmlhttp://www.airspayce.com/mikem/arduino/AccelStepper/index.html">
   AccelStepper library</a> being present on your system. Please make sure you
   have installed the latest version before using this firmware.

   @section license License

   Licensed under the GPLv3.

*/

#define RATIO              54    ///< Gear ratio of rotator gear box
#define MICROSTEP          16     ///< Set Microstep
#define MIN_PULSE_WIDTH    1    ///< In microsecond for AccelStepper
#define MAX_SPEED          6400  ///< In steps/s, consider the microstep
#define MAX_ACCELERATION   3200  ///< In steps/s^2, consider the microstep
#define SPR                3200 ///< Step Per Revolution, consider the microstep 200steps(1.8 deg)*16microsteos
#define MIN_M1_ANGLE       0     ///< Minimum angle of azimuth
#define MAX_M1_ANGLE       360   ///< Maximum angle of azimuth
#define MIN_M2_ANGLE       0     ///< Minimum angle of elevation
#define MAX_M2_ANGLE       180   ///< Maximum angle of elevation
#define DEFAULT_HOME_STATE HIGH  ///< Change to LOW according to Home sensor
#define HOME_DELAY         12000 ///< Time for homing Deceleration in millisecond

#include <AccelStepper.h>
#include <TMCStepper.h>
#include <Wire.h>
#include "globals.h"
#include "easycomm.h"
#include "rotator_pins.h"
#include "rs485.h"
#include "endstop.h"
#include "watchdog.h"

uint32_t t_run = 0; // run time of uC

#define AZ_DRIVER_ADDRESS 0b00 // TMC2209 Driver address according to MS1 and MS2
#define EL_DRIVER_ADDRESS 0b01 // TMC2209 Driver address according to MS1 and MS2
#define R_SENSE 0.11f // Match to your driver


easycomm comm;
TMC2209Stepper driver_az(&Serial1, R_SENSE, AZ_DRIVER_ADDRESS);
TMC2209Stepper driver_el(&Serial1, R_SENSE, EL_DRIVER_ADDRESS);
AccelStepper stepper_az(1, M1IN1, M1IN2);
AccelStepper stepper_el(1, M2IN1, M2IN2); //stepper.DRIVER
endstop switch_az(SW1, DEFAULT_HOME_STATE), switch_el(SW2, DEFAULT_HOME_STATE);
wdt_timer wdt;

enum _rotator_error homing(int32_t seek_az, int32_t seek_el);
int32_t deg2step(float deg);
float step2deg(int32_t step);

void setup() {
  // Homing switch
  switch_az.init();
  switch_el.init();

  // Serial Communication
  comm.easycomm_init();
  Serial1.begin(19200);//Enable talking to tmc drivers

  driver_az.begin();             // Initiate pins and registeries
  driver_az.toff(5);                 // Enables driver in software
  driver_az.rms_current(1700, 0.5);    // Set stepper current to 600mA. The command is the same as command TMC2130.setCurrent(600, 0.11, 0.5);
  driver_az.pwm_autoscale(true);
  driver_az.microsteps(MICROSTEP);
  driver_az.intpol(true); //Interpolate to 256microsteps
  driver_az.en_spreadCycle(true);

  driver_el.begin();             // Initiate pins and registeries
  driver_el.toff(5);                 // Enables driver in software
  driver_el.rms_current(1700, 0.5);    // Set stepper current to 600mA. The command is the same as command TMC2130.setCurrent(600, 0.11, 0.5);
  driver_el.pwm_autoscale(true);
  driver_el.microsteps(MICROSTEP);
  driver_el.intpol(true); //Interpolate to 256microsteps
  driver_el.en_spreadCycle(true);

  // Stepper Motor setup
  stepper_az.setEnablePin(MOTOR_EN);
  stepper_az.setPinsInverted(false, false, true);
  stepper_az.enableOutputs();
  stepper_az.setMaxSpeed(MAX_SPEED);
  stepper_az.setAcceleration(MAX_ACCELERATION);
  stepper_az.setMinPulseWidth(MIN_PULSE_WIDTH);
  
  stepper_el.setPinsInverted(false, false, true);
  stepper_el.enableOutputs();
  stepper_el.setMaxSpeed(MAX_SPEED);
  stepper_el.setAcceleration(MAX_ACCELERATION);
  stepper_el.setMinPulseWidth(MIN_PULSE_WIDTH);

  // Initialize WDT
  wdt.watchdog_init();
}

void loop() {
  // Update WDT
  wdt.watchdog_reset();

  // Get end stop status
  rotator.switch_az = switch_az.get_state();
  rotator.switch_el = switch_el.get_state();

  // Run easycomm implementation
  comm.easycomm_proc();

  // Get position of both axis
  control_az.input = step2deg(stepper_az.currentPosition());
  control_el.input = step2deg(stepper_el.currentPosition());

  // Check rotator status
  if (rotator.rotator_status != error) {
    if (rotator.homing_flag == false) {
      // Check home flag
      rotator.control_mode = position;
      // Homing
      rotator.rotator_error = homing(deg2step(-MAX_M1_ANGLE),
                                     deg2step(-MAX_M2_ANGLE));
      if (rotator.rotator_error == no_error) {
        // No error
        rotator.rotator_status = idle;
        rotator.homing_flag = true;
      } else {
        // Error
        rotator.rotator_status = error;
        rotator.rotator_error = homing_error;
      }
    } else {
      // Control Loop
      stepper_az.moveTo(deg2step(control_az.setpoint));
      stepper_el.moveTo(deg2step(control_el.setpoint));
      rotator.rotator_status = pointing;
      // Move azimuth and elevation motors
      stepper_az.run();
      stepper_el.run();
      // Idle rotator
      if (stepper_az.distanceToGo() == 0 && stepper_el.distanceToGo() == 0) {
        rotator.rotator_status = idle;
      }
    }
  } else {
    // Error handler, stop motors and disable the motor driver
    stepper_az.stop();
    stepper_az.disableOutputs();
    stepper_el.stop();
    stepper_el.disableOutputs();
    if (rotator.rotator_error != homing_error) {
      // Reset error according to error value
      rotator.rotator_error = no_error;
      rotator.rotator_status = idle;
    }
  }
}

/**************************************************************************/
/*!
    @brief    Move both axis with one direction in order to find home position,
              end-stop switches
    @param    seek_az
              Steps to find home position for azimuth axis
    @param    seek_el
              Steps to find home position for elevation axis
    @return   _rotator_error
*/
/**************************************************************************/
enum _rotator_error homing(int32_t seek_az, int32_t seek_el) {
  bool isHome_az = false;
  bool isHome_el = false;

  // Move motors to "seek" position
  stepper_az.moveTo(seek_az);
  stepper_el.moveTo(seek_el);

  // Homing loop
  while (isHome_az == false || isHome_el == false) {
    // Update WDT
    wdt.watchdog_reset();
    if (switch_az.get_state() == true && !isHome_az) {
      // Find azimuth home
      stepper_az.moveTo(stepper_az.currentPosition());
      isHome_az = true;
    }
    if (switch_el.get_state() == true && !isHome_el) {
      // Find elevation home
      stepper_el.moveTo(stepper_el.currentPosition());
      isHome_el = true;
    }
    // Check if the rotator goes out of limits or something goes wrong (in
    // mechanical)
    if ((stepper_az.distanceToGo() == 0 && !isHome_az) ||
        (stepper_el.distanceToGo() == 0 && !isHome_el)) {
      return homing_error;
    }
    // Move motors to "seek" position
    stepper_az.run();
    stepper_el.run();
  }
  // Delay to Deccelerate and homing, to complete the movements
  uint32_t time = millis();
  while (millis() - time < HOME_DELAY) {
    wdt.watchdog_reset();
    stepper_az.run();
    stepper_el.run();
  }
  // Set the home position and reset all critical control variables
  stepper_az.setCurrentPosition(0);
  stepper_el.setCurrentPosition(0);
  control_az.setpoint = 0;
  control_el.setpoint = 0;

  return no_error;
}

/**************************************************************************/
/*!
    @brief    Convert degrees to steps according to step/revolution, rotator
              gear box ratio and microstep
    @param    deg
              Degrees in float format
    @return   Steps for stepper motor driver, int32_t
*/
/**************************************************************************/
int32_t deg2step(float deg) {
  return (RATIO * SPR * deg / 360);
}

/**************************************************************************/
/*!
    @brief    Convert steps to degrees according to step/revolution, rotator
              gear box ratio and microstep
    @param    step
              Steps in int32_t format
    @return   Degrees in float format
*/
/**************************************************************************/
float step2deg(int32_t step) {
  return (360.00 * step / (SPR * RATIO));
}

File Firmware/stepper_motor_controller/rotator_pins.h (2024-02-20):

/*!
* @file rotator_pins.h
*
* It is a header file for pin mapping.
*
* Licensed under the GPLv3
*
*/

#ifndef ROTATOR_PINS_H_
#define ROTATOR_PINS_H_

#define M1IN1 10 ///< Motor 1 PWM pin
#define M1IN2 9  ///< Motor 1 PWM pin
#define M1SF  7  ///< Motor 1 digital input, status flag
#define M1FB  A1 ///< Motor 1 analog input, current/load feedback

#define M2IN1 11 ///< Motor 2 PWM pin
#define M2IN2 3  ///< Motor 2 PWM pin
#define M2SF  6 ///< Motor 2 digital input, status flag
#define M2FB  A0 ///< Motor 2 analog input, current/load feedback

#define MOTOR_EN 8 ///< Digital output, to enable the motors

#define SW1 5 ///< Digital input, to read the status of end-stop for motor 1
#define SW2 4 ///< Digital input, to read the status of end-stop for motor 2

#define RS485_DIR 2 ///< Digital output, to set the direction of RS485 communication

#define SDA_PIN 3 ///< I2C data pin
#define SCL_PIN 4 ///< I2C clock pin

#define PIN12 12 ///< General purpose I/O pin
#define PIN13 13 ///< General purpose I/O pin
#define A2    A2 ///< General purpose I/O & analog pin
#define A3    A3 ///< General purpose I/O & analog pin

#endif /* ROTATOR_PINS_H_ */
